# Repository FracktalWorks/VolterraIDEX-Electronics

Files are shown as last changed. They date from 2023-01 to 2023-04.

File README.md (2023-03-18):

# VolterraIDEX-Electronics
Pin Configurations, EagleCAD and gerber files for Volterra IDEX PCBs

The following documentation contains the contents about the pin connections, firmware configurations of the BigTreeTech Octopus V1.1 which is assembled into the VolterraIDEX model of 400x400x370 buildsize.

## Initial Preparation
set jumpers as shown:


Green – Add Jumper

Red – Remove Jumper

1. Insert only the jumper in the Green and remove the other three jumpers in the Red in order to use TMC2209 UART mode.
2. Remove all the jumpers of DIAG to avoid the influence of TMC2209 DIAG on the endstop.
3. Remove the USB 5V power supply jumper to avoid the interaction between the USB 5V of raspberry pi and the DC-DC 5V of the motherboard.
4. Insert all the jumpers into V_FUSED to set the fan voltage to the system supply voltage.
5. Insert the jumper into V_FUSED to set the probe voltage to the system supply voltage.

## Wiring
1. Connect 24V and GND (V+ and V-) from the PSU to PWR and MOTOR_POWER
2. Connect the X(L) Motor (gantry left) to MOTOR0
3. Connect the X(R) Motor (gantry right) to MOTOR1 
4. Connect the E0 (Left Extruder front) motor to MOTOR2_1
5. Connect the E0' (Left Extruder back) motor to MOTOR2_2
6. Connect the Z motor to MOTOR3
7. Connect the Y (gantry left) to MOTOR4
8. Connect the Y1 (gantry right) to MOTOR5
9. Connect the E1 (Right Extruder front) to MOTOR6
10. Connect the E1' (Right Extruder back) to MOTOR7
11. Connect the Extruder0 hot end heater to HE0
12. Connect the Extruder1 hot end heater to HE1
13. Connect the bed SSR (DC Control Side) to HE2
14. Connect the Chamber SSR (DC Control Side) to HE3
Octopus pins and wirings

Bed Heater and Chamber SSR Connections

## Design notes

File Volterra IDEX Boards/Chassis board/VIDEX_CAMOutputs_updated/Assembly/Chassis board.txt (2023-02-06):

Partlist exported from C:/Users/nishb/OneDrive/Documents/GitHub/VolterraIDEX-Electronics/Volterra IDEX Boards/Chassis board/Chassis board.sch at 06-02-2023 11:02

Qty Value                          Device                         Package                    Parts                                                                                                                     Description              
3   FFC/FPC/34PIN/1MMPITCH/TOPLOCK FFC/FPC/34PIN/1MMPITCH/TOPLOCK 34PIN/1MMPITCH/FFC/FPC     K1, K2, K3                                                                                                                                         
1   FRACKTALLOGO                   FRACKTALLOGO                   FRACKTALLOGO               U$2                                                                                                                                                
1   FRAME-LETTER                   FRAME-LETTER                   CREATIVE_COMMONS           FRAME1                                                                                                                    Schematic Frame - Letter 
1   JST-XH-02-PIN-LONG-PAD         JST-XH-02-PIN-LONG-PAD         JST-XH-02-PACKAGE-LONG-PAD X1                                                                                                                        JST XH Connector 2 Pin   
22  TEST-POINTTP_15TH_THRU         TEST-POINTTP_15TH_THRU         TP_15TH                    TP1, TP2, TP3, TP4, TP5, TP6, TP7, TP8, TP9, TP10, TP11, TP12, TP13, TP14, TP15, TP16, TP17, TP18, TP19, TP20, TP21, TP22 SparkFun Test Points

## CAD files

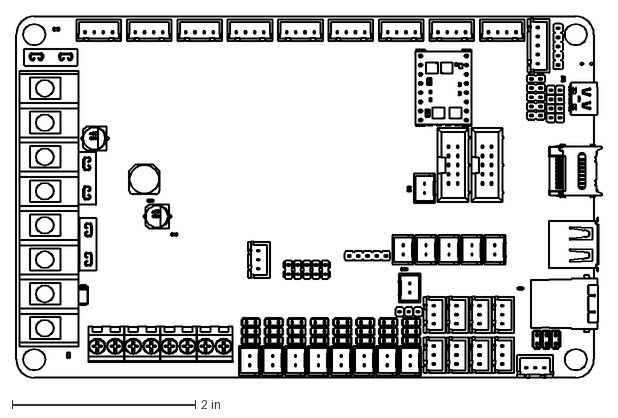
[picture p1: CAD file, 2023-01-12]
BIGTREETECH Octopus V1.0-1.dxf
6.39 x 3.94 in

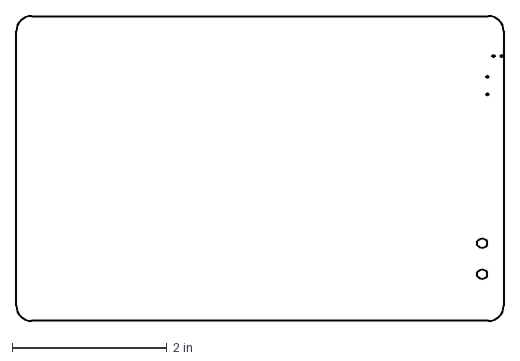
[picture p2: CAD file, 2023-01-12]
BIGTREETECH base Octopus V1.0-1.dxf
6.30 x 3.94 in

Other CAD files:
3D Board/BIGTREETECH Octopus V1.0-1.dwg
3D Board/0411-2.iam
3D Board/1.iam
3D Board/1.ipt
3D Board/1001-3.ipt
3D Board/1001-8.ipt
3D Board/100UF35V.iam
3D Board/2.ipt
3D Board/220UF35V.iam
3D Board/254-3X2.iam
3D Board/254-3X4-1.iam
3D Board/254-4X2.iam
3D Board/266863104.iam
3D Board/2P-254.iam
3D Board/2P-254.ipt
3D Board/3.ipt
3D Board/3P-254.iam
3D Board/4.ipt
3D Board/5.ipt
3D Board/500156144.iam
3D Board/500156144_1.iam
3D Board/500156144_2.iam
3D Board/500156144_3.iam
3D Board/500160368.iam
3D Board/500901-0801_1.ipt
3D Board/5555140-1.iam
3D Board/587257496.iam
3D Board/5P-254.iam
3D Board/5X2P-254.iam
3D Board/6.ipt
3D Board/6641437008.iam
3D Board/6641437328.iam
3D Board/6641440128.iam
3D Board/6641441328.iam
3D Board/6641441568.iam
3D Board/6641441808.iam
3D Board/6641442208.iam
3D Board/6641442768.iam
3D Board/6641443168.iam
3D Board/70314708_1.ipt
3D Board/71071830_1.ipt
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

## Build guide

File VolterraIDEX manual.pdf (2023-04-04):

# USER MANUAL

Disclaimer
Please read the user manual and contents of the instructions carefully. Failing to read the user guide may lead to injuries and damage to Volterra, Industrial 3D Printer. Users of the printer should understand the contents of the manual completely before starting up the Volterra printer**.The methods or conditions used for assembling, handling, storage, use or disposal of the machine are beyond our control or beyond our knowledge. For this reason and other reasons, we do not assume responsibility and explicitly disclaim liability for the loss, injuries, expenses or damage arising out of or in any way connected with the assembly, handling, storage, use or disposal of the product.
The document was made from sources which we believe are reliable. However, the information is provided without any warranty, express or implied, regarding its correctness.

Intended use of Volterra
Volterra 3D Printers are designed and crafted for fused deposition modeling process intended with engineering thermoplastics within a commercial/ business/ research environment. The blend of the precision and speed makes the Volterra 3D printers the perfect machines to conceptualize models, prototypes and small series of production. The printer is coupled with Fracktory Desktop to provide the best experience in slicing with easy interface for the user to change the material properties such that it matches with the machine settings. Fracktory is specifically designed for Volterra printers and gives enhanced experience to the user.
** Volterra printer refers to Volterra family of printers

Preface
This is the installation and user manual for your Volterra 3D printer. This manual contains chapters about the installation and use of the Volterra 3D printer. Important information and instructions on safety, installation and use have been emphasized in this manual. Please read all information and follow the instructions and guidelines in this manual carefully. This ensures that you will obtain great quality prints and that possible accidents and injuries will be prevented. Make sure the user of the Volterra has access to this manual.
Every effort has been made to make this manual complete and accurate as possible. The information is believed to be true but does not aim to be all inclusive and shall be used only as a guide. Kindly bring us the attention on any errors or omissions, so that we can make amendments. Revision and improvement of the documentation could help you serve better.

### Contents

1. Product Details | 2
2. Introduction | 3
3. Getting Started | 5
4. Safety | 7
5. Ancillary Features | 9

### 6. Specifications

11
7. What‘s in the box | 12
8. Setting up | 14
9. Startup process | 17
1O. Downloading and Installing | 27
11. Printing | 31

# WELCOME

# LET’S START

1. PRODUCT DETAILS
Volterra Manual | Page |2

### 1 Product Details

Title: Volterra machine series
Filament diameter: 1.75 mm
Manufacturer: Fracktal Works Pvt Ltd
Manufacturer address: No. 3, 50ft Laggere Main Road Chowdeshwari Nagara, Near Old Police Chowky, Bengaluru, Karnataka, 560 058 Power supply voltage: 200V, 50Hz
Power consumption: 1900W
Working temperature range: 18 °C - 38 °C, indoor use only Working humidity: 85 % or less

2. INTRODUCTION
Volterra Manual | Page |3

### 2 Introduction

Thank you for purchasing our Volterra from Fracktal Works. For correct service of the printer, please read the handbook carefully. All the chapters contain valuable information for the proper service usage.
The user manual is designed specially to make your journey with Volterra printers smooth and hassle free. Fracktal Works welcomes you to the exciting era of 3D printing using Volterra. Read and follow this guide to get the best out of your machine and for an amazing 3D printing experience.

# GETTING STARTED

kknhg

3. GETTING STARTED

### 3 Getting Started

Volterra can print solid 3D models which are simple or complicated ranging from toys to bearings, machine parts, replacements of broken article, casing and variety of other things. Volterra helps turn concepts and ideas into physical prototypes saving time, reducing costs and shortening product development life cycles.
Printing solid 3D objects is an additive manufacturing process which involves a few simple steps. Initially a digital file or a solid model is prepared. This model is then imported into a software commonly known as a ‘Slicer’ and is sliced into layers and fed into the printer to get the model printed. The printer prints by depositing molten material layer by layer with the help of a 3-axis manipulator.

# SAFETY

4. SAFETY

### 4 Safety

### 4.1 Electric Shock Hazards

Never open the access panel when there is power supply to the printer. Before removing the electronics casing always power down the printer completely, Also unplug the power cord connected to the printer. Allow the power supply to discharge for at least one minute.

### 4.2 Burn Hazard

Never touch the extruder nozzle or heater block without turning off the hot end and allowing it to completely cool down naturally. The hot end could take up to twenty minutes to completely cool. Also never touch the plastic which was just extruded. Wait for at least 3 minutes for it to cool down naturally. The plastic can stick to your skin and cause burns. Beware of the heated bed which can reach high temperatures and is capable of causing burns.

### 4.3 Fire Hazard

Never place flammable materials or liquids on or near the printer when powered or in operation.

### 4.4 Pinch Hazard

When the printer is in operation, if placed near the moving parts including the belts, pulleys, or gears, take care of your fingers. Also, tie back long hair or clothing that could get caught in the moving parts of the printer.

### 4.5 Static Charge

Make sure to ground yourself before touching the printer, especially with the electronics. Electrostatic charge can damage electronic components and may affect its functionality. To ground yourself, touch any grounded source.

### 4.6 Age Warning

For users under the age of 18, adult supervision is recommended. Beware of choking hazards.

### 4.7 Fumes and smell Warning

While printing filaments such as ABS, fumes are produced. Do not inhale the fumes because they are toxic in nature. Fumes released could contain toxic substances known as VOC‘s (Volatile Organic compound). Not all VOC‘s are actually toxic, but some may be, especially for younger users. Machine is to be placed in a well ventilated area.

Volterra Manual | Page |7

# ANCILLARY FEATURES

### 5. ANCILLARY FEATURES

### 5 Ancillary Features

5. 1 HEPA Filter

HEPA filter is mounted on the central rear panel of the machine which is mechanically convicting the air through a fine mesh that traps harmful particulate air.

### 5.2 IDEX technology

IDEX is the extrusion system capable of printing with two heads independently. This allows enabling Duplication and Mirror printing modes capable of printing two pieces at a time. Double printing capacity means double productivity, all with the same investment.

### 5.3 Chamber heaters

Chamber heaters enables users to print in high temperature filaments, such as PEEK and ULTEM which need a stable chamber temperatures.

### 5.4 Filament heaters

Filament materials such as PVA absorbs moisture when stored in open atmosphere. It is essential for PVA to be preheated before giving print. Instead of preheating externally, filament heater eliminates the use of external heating.

### 5.5 Light Tower

Stack lights are used in a variety of machines and process environments. Color codes for our machine is as follows:

- Green indicates “Printing"
- Amber indicates “Operational/ Idle"
- Red indicates “Error/ Offline / any other issue"

# Specification & what’s in

# the box!

6. SPECIFICATIONS

### 6 Specifications

| Parameters | Speed | IDEX | HT
- | Technology | FDM/FFF | FDM/FFF | FDM/FFF
- | Model Materials | PLA, ABS, Nylon Flexible** | PLA, PVA, ABS, HIPS, Flexible** | PLA, ABS, Nylon, ULTEM, PEEK, Flexible**
- | Layer Resolution | 100 – 450 um | 100 – 450 um | 100 – 450 um
- | Positioning Accuracy Z | 5 um | 5 um | 5 um
- | Positioning Accuracy X-Y | 10 um | 10 um | 10 um
- Max. Print Size Heated
| With “Magnalock Build Substrate” | 380x400x400 mm | 380x400x400 mm | 380x400x400 mm
- | Chamber Heater | Yes (120C) | Yes (120C) | Yes (150C)
- | Filament Heater | Yes (60C) | Yes (60C) | Yes (60C)
- | Camera | Live Camera for 5MP | Live Camera for 5MP | Live Camera for 5MP
- | Heated Bed | Yes (120C) | Yes (120C) | Yes (150C)*
- | Max. Nozzle temperature | 250C | 250C | 450C
- | Door Sensor | Yes (Active Detection) | Yes (Active Detection) | Yes (Active Detection)
- | Nozzles*** | 1 (0.6mm Default) | 2 (0.6mm Default) | 2 (0.6mm Default)
- | File Type | STL, OBJ, G-Code | STL, OBJ, G-Code | STL, OBJ, G-Code
- | HEPA Filter | Yes | Yes | Yes
- | Power | 240V, 60Hz, 1900W* | 240V, 60Hz, 1900W* | 240V, 60Hz, 1900W*
- 7” “Mission Control:
| Touch” Panel | Touch HMI | Touch HMI | Touch HMI
- Tower Light Indication
| and Emergency Stop Switch | Yes | Yes | Yes
- | Interface Connectivity | USB, Wi-Fi, Ethernet | USB, Wi-Fi, Ethernet | USB, Wi-Fi, Ethernet

*Specification tend to change as per design
** Machine ships with Brass-0.6mm nozzles Extra nozzles(0.25, 0.4, 0.6, 0.8) are charged additionally. Nozzle material with Hardened Steel and Stainless Steel variants are also available
*** Compatible with Fracktal Works Flex series of Filaments
**** Comprehensive warranty covers all parts except nozzle assembly, accessory box tools and consumables

7. WHAT‘S IN THE BOX

### 7 What‘s in the box

(a) Light tower
(b) Hotend and Nozzle kits*
(c) Filament*
(d) Camera*

Accessories Checklist

1. Flex Build Plate attached to the bed
2. Allen Keys (2, 2.5, 3 mm size)
3. Print Adhesive
4. WD 40 Spray
5. USB drive
6. Nozzle cleaning tool or stove pin
7. Power cord
8. Sharp Tweezers
9. Filament cutter

*Few accessories are subjected to purchase order

# SETTING

UP

8. SETTING UP

### 8 Setting up

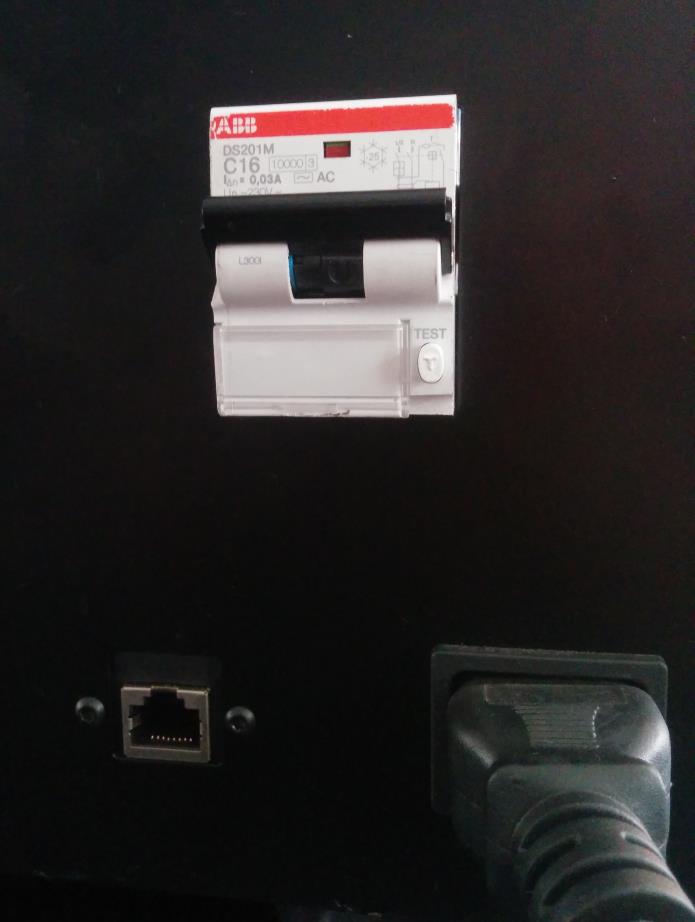
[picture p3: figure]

Figure 8.1: RCBO contactor with socket

The power cord has to be connected to the IEC socket located at the backside in the bottom left of the printer near the power socket. Connect the power cable to the 220V wall socket and flip the contactor (RCBO) to turn the printer ON.
After turning the printer ON, turn the button switch ON which is located on front panel of the printer. An LED should light up after pressing the switch. LED lighting can signify the power state of the printer. When the button switch is in pressed condition, it signifies the printer is in ON condition also showing with ON state of the LED on the button switch. On the other way, when the button switch is in released position, the LED light should go OFF and state the turned off condition.
By turning the two switches, the printer should boot up and the display should show the booting. Make sure the emergency stop button is in release position.
The E-stop or the Kill switch turns off the whole machine. This switch is a handy add-on in case
of emergency.
In case, you want the printer to be connected to a wired LAN connection, the LAN cable can be connected to the LAN port present just beside the power socket.

8. SETTING UP

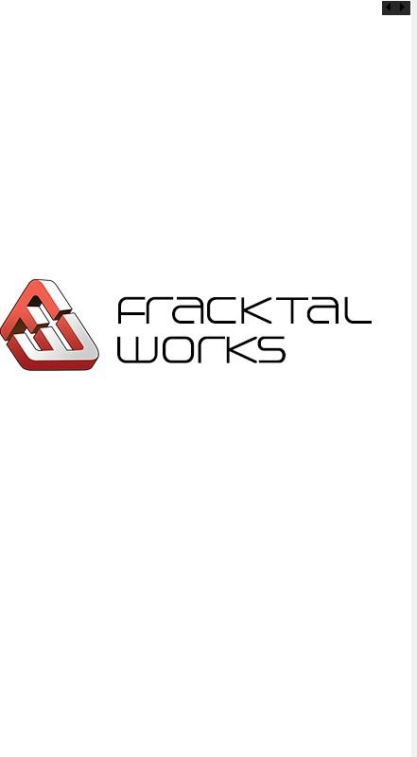
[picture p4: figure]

Figure 8.2: Fracktal Works Loading Screen .

# STARTUP PROCESS

9. STARTUP PROCESS

### 9 Startup process

After turning on the power supply for Volterra, the LCD screen will get activated. The following section of the manual will guide you through the process of loading the filament, leveling the print plate and testing your first build.
First you mount the magnetic print plate on the bed and it will automatically stick to it. Note that the slits on the build plate (highlighted) pass through the mounts on the bed.

Figure 9.1: Build surface aligning with the slits/notches on bed

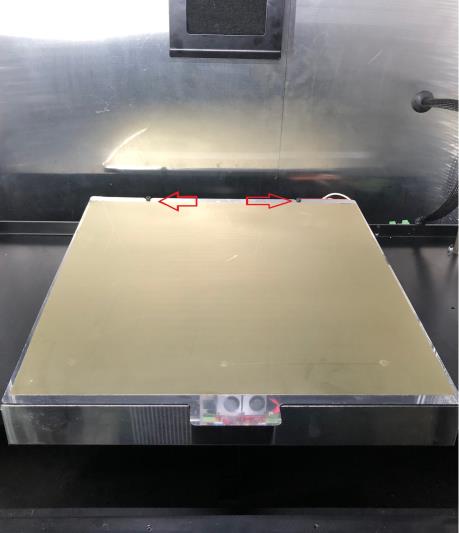
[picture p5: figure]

Figure 9.2: Build surface placed on the bed

Your bed should ultimately look something like this.

9. STARTUP PROCESS
9. 1 Loading Filament

To load a new filament, select the control option from the main menu and click on the following icon.

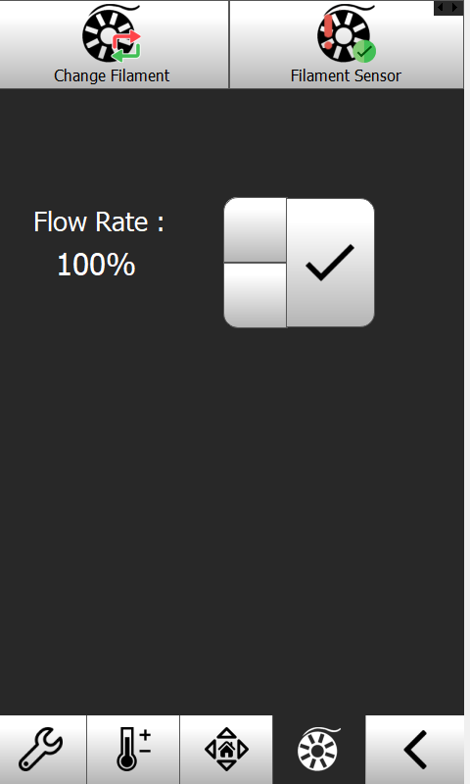
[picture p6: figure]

Figure 9.3: Change filament control

9. STARTUP PROCESS

Figure 9.4: change filament button

Press on the ‘change filament’ button on corner as shown in fig. 9.4.
If you have VolterraIDEX, the filament change wizard screen should look something like the image shown in fig 9.5.

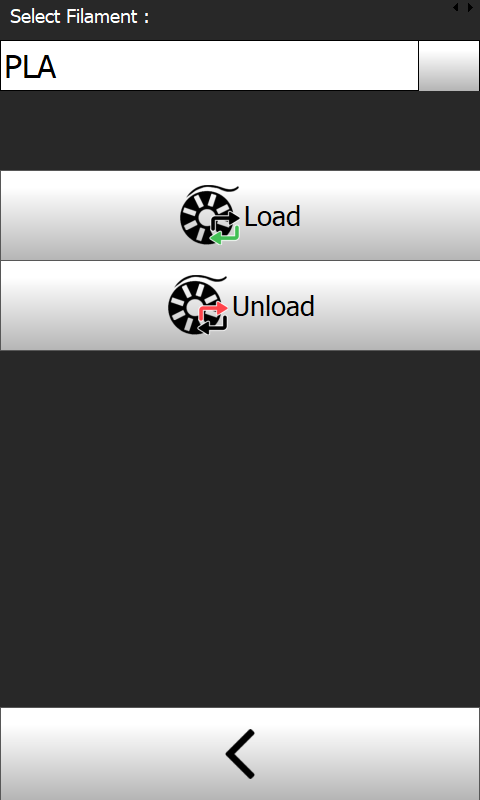
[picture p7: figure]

Figure 9.5: Change filament menu for VolterraIDEX

9. STARTUP PROCESS

Figure 9.6: Change filament menu for VolterraIDEX

From the drop down menu under "Select Filament", select the filament which you want to load and tap on Load button.
If you have VolterraIDEX (Fig 9.6), the filament change wizard screenshould look something like the image above.

9. STARTUP PROCESS

From the drop down menu under "Select Filament", select the filament which you want to load. Also select the nozzle into which you want to insert the filament and tap on Load button. For example, if you want to print PLA. Select PLA from the select drop down menu.
If the old filament is already loaded, then press the unload icon and when the filament is out press the load filament icon to insert the new filament. You can tap on unload again for unloading the filament in case the filament is not unloaded in one tap.

9. STARTUP PROCESS

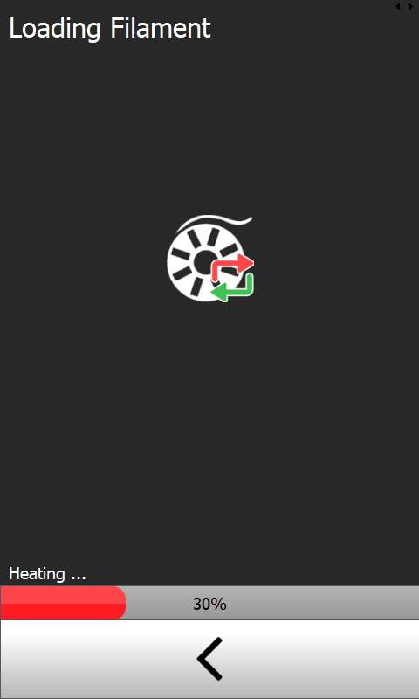
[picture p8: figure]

Figure 9.8: Change filament Heating process

When you press the load icon the printer should start heating the extruder to facilitate the loading of the filament and the window should look like the image shown above as per fig 9.8.
Once the extruder is heated according to the type of filament required, another window should appear which looks like the image shown in fig 9.9.

9. STARTUP PROCESS

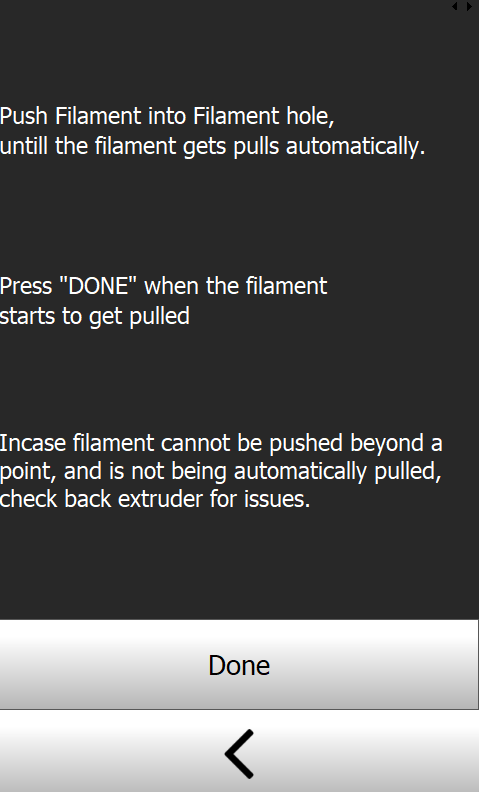
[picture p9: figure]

Figure 9.9: Change Filament Heating Process

In this window, Insert the filament into the channel present in the filament chamber. The left side channel is for EXT0 and the right side channel is for EXT1. Keep pushing into the channel and the PTFE till it reaches the back side extruder motor and gets pulled by it automatically, since the motor keeps rotating continuously. If the filament does not get pulled despite pushing to its limit, do check the back extruder to check if any issues persists such as, getting stuck in the PTFE or getting stuck in the motor arm.
After the Filament gets pulled successfully, press “DONE” on the screen. The filament gets pulled with a faster federate.

9. STARTUP PROCESS

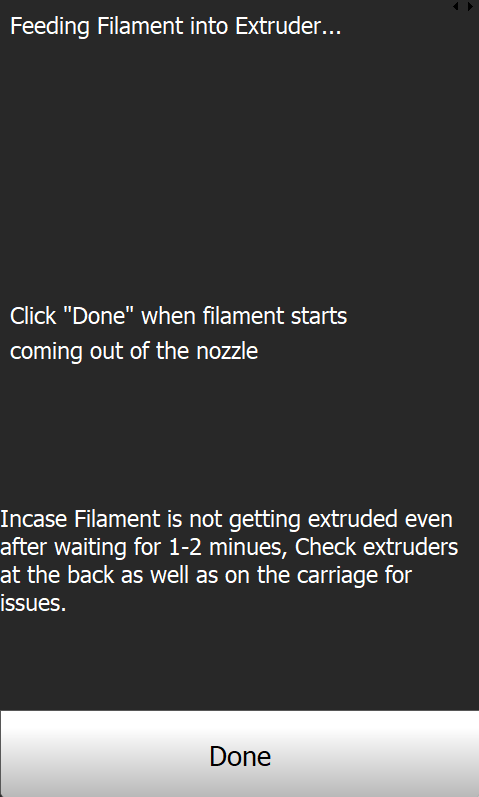
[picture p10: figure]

Figure 9.10: Change Filament Heating Process #2

When the filament gets pulled with a faster federate, and when the filament starts coming out of the nozzle, click on “DONE”. In cases when the filament does not come out of the nozzle waiting for approximately 1 – 2 minutes, do check the extruders at the back and as well as the carriage extruders if any issues persists.

9. STARTUP PROCESS

### 9.2 Levelling the bed

Importance of bed levelling
Volterra has gone through the process of bed levelling at Fracktal Works. However, there is a
chance that the alignment is disturbed during the transportation and unboxing process.
If the extruder nozzle is too far from the build platform, or if all parts of the build plate are not at the same distance from the nozzle while printing, then the build will not attach properly on the build surface. If the extruder nozzle is too close to the build platform, then the filament might be prevented from being extruded and it could also lead to scratches on the build plate.

Levelling the build plate ensures that the objects you print adhere well to the build plate, to give you a hassle free and smooth experience.
The Process of Levelling and Testing your first print
Note: Make sure there is no plastic sticking out of the nozzle. It is recommended to heat the nozzle and remove any excess plastic using supplied tweezers before continuing.
To initiate Bed Levelling, on the home screen, click on | icon to open the main menu.

9. STARTUP PROCESS

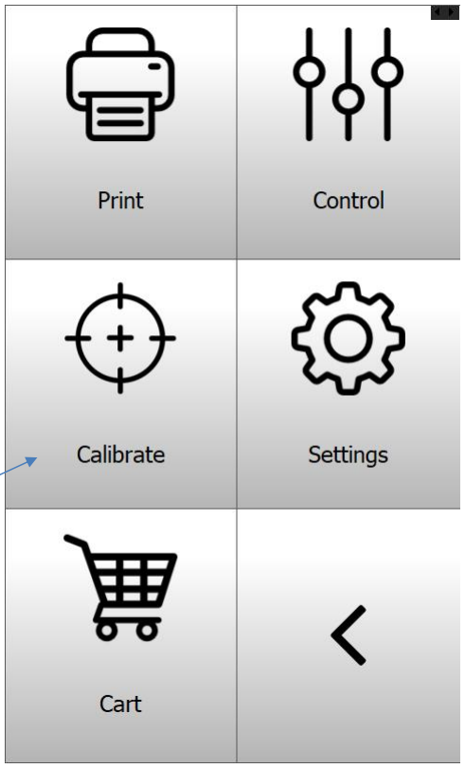
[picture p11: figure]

Figure 9.10: Main Menu

From there select the menu icon, after clicking on the menu icon, a new screen should come up
which looks like the image shown above. From the menu select the Calibrate icon and that will take you to the calibration panel. The calibration panel should look like in Fig 9.11.

9. STARTUP PROCESS

Figure 9.11: Main Menu

From that screen select the Calibration Wizard option and follow the on screen instructions that follow up
and you will have a perfectly leveled bed for your printer.

# DOWNLOADING AND INSTALLING

10. DOWNLOADING AND INSTALLING

### 1O Downloading and Installing

The preferred software for your Volterra printer is Fracktory 3 from Fracktal Works. This software package converts your 3D model(STL file) into instructions(G-code file) that your Volterra requires to produce an object.

- The Fracktory software package can be downloaded from fracktal.in
- Download the latest version of Fracktory for your operating system.
- Note: You will require a 64 bit system to run Fracktory.
- Open the installer and follow the directions to install the software.
- After installing Fracktory, open the application to configure the software to your 3D printer.

1O.1 Adjusting the model

There are various ways to manipulate the object before printing like rotation, scaling and mirroring along axis.

1O.1.1 Rotate

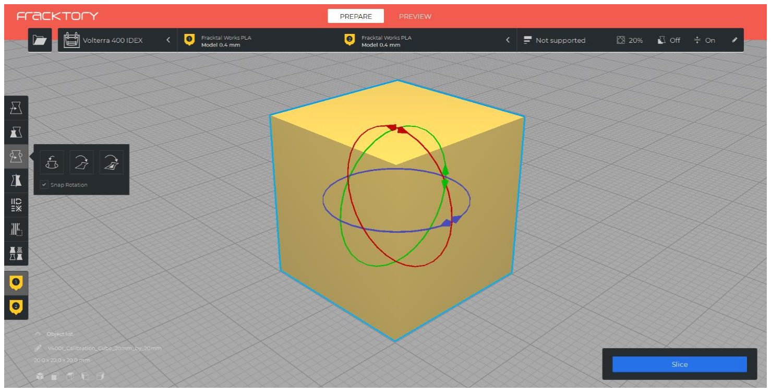
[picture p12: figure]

Figure 10.1: Fracktory rotate option

The icon on the left side shows the rotate button; it allows you to rotate the model in the X, Y or Z axes. By selecting one of the axes and on moving your mouse, you can rotate the object with an angleof 15 degrees.

10. DOWNLOADING AND INSTALLING

You can also rotate the object with an angle of 1 degree by holding the “Shift” Key.
Once the rotate button has been selected a few more options will pop up just above the rotate button. The “Reset” button offers the possibility to resets the model to its original position. By using the “Lay flat” option your model will be placed flat on the surface of the build plate. This can become handy when your model doesn’t have a completely flat surface or when it doesn’t load correctly in Fracktory. The model will be placed on the face closest to the build plate.

1O.1.2 Scale

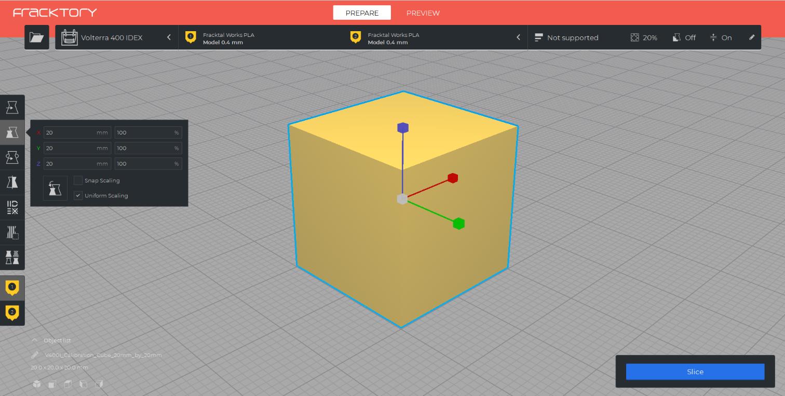
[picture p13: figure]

Figure 10.2: Fracktory scale option

The middle icon is the Scale button. This option can be used to change the dimensions of the model in X, Y and Z direction. Scaling can be done by clicking and dragging the (square) scaling icons that appear on the model, or by changing the numeric values that appear in the box just above the "Scale" button. You can either use a scale factor to change the dimensions or enter the exact size. A model will be scaled in all directions, simultaneously by default, but you can unmark “Uniform scale” in order to scale in each direction independently. Furthermore a “Reset” and “Scale to max” button will be shown above the Scale button. The Reset button allows you to reset the model to its original dimensions. By using the Scale to max option, the model will be scaled to the maximum size that fits in the machine.

10. DOWNLOADING AND INSTALLING

1O.1.3 Mirror

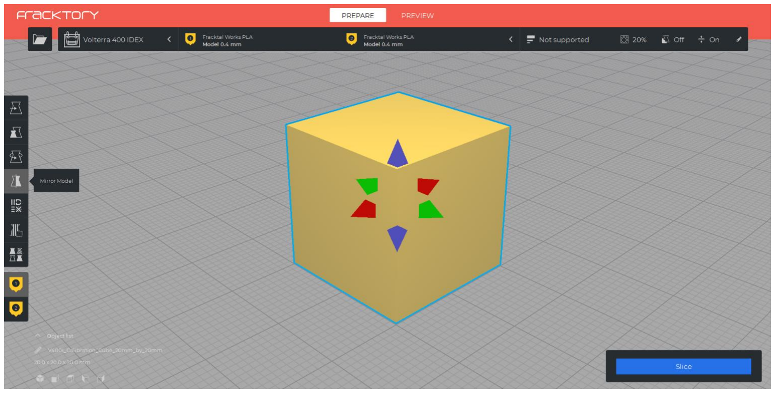
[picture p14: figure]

Figure 10.3: Fracktory mirror option

The right most icon at the bottom is the “Mirror” button. This can be used to flip the model in either the X, Y or Z direction.

# PRINTING

11. PRINTING

### 11 Printing

Now that you have installed and configured Fracktory, you can print your first part. Some sample files are provided in the supplied SD card. Fracktory uses millimeters as the base unit. When adding any files please check that the units are correct by clicking on the scale button.

Click the load Button and select the required “.STL” file for printing.
Now your object will be placed in center. You can manipulate the object using move, scale, rotate etc.

Figure 11.1: Fracktory loaded with STL for printing

Whenever you load a model, adjust a model or change settings, Fracktory starts processing the file on-the-fly.

You can see its progress below save G-code button. G-code is the processed file requiredby the machine to print your 3D object. When the file is processed you click the save G-code button. If you have inserted a SD card then the button turns into a SD card button. This will load the G-code directly into the SD card. Beware that it will overwrite the previous file of same name without warning.
When G-code file is generated it is saved on your system and can be used to print using Wi-Fi or USB mass storage device

11. PRINTING

If Printing from Wi-Fi then follow the below steps

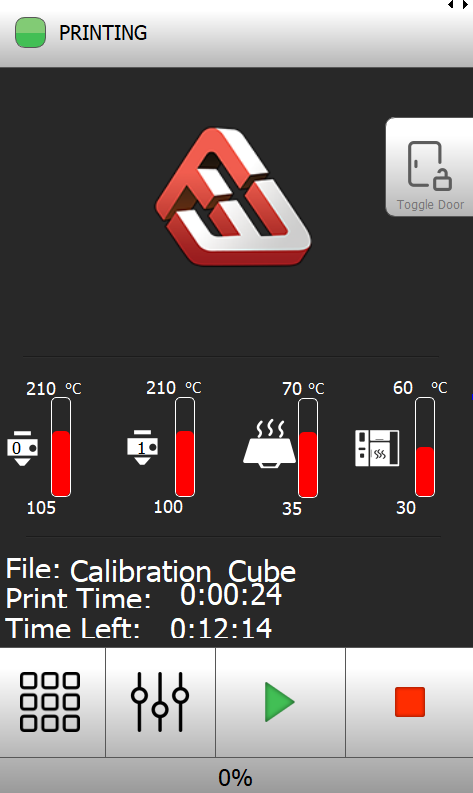
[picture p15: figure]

Figure 11.2: printing

When running the printer for the first time select the menu bar from the main screen. Open and select the settings icon in it.

11. PRINTING

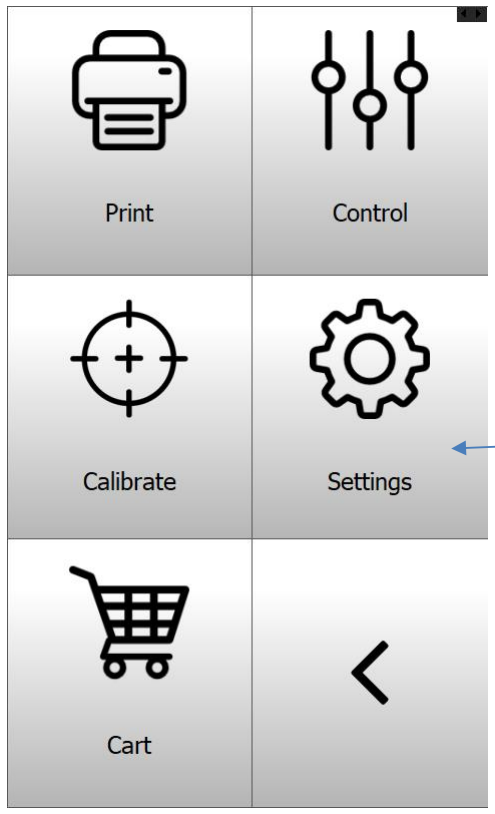
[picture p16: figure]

Figure 11.3: Menu UI in printer

When you select the settings icon, this window should open Then click on Configure Wi-Fi icon (in Figure 11.3)

11. PRINTING

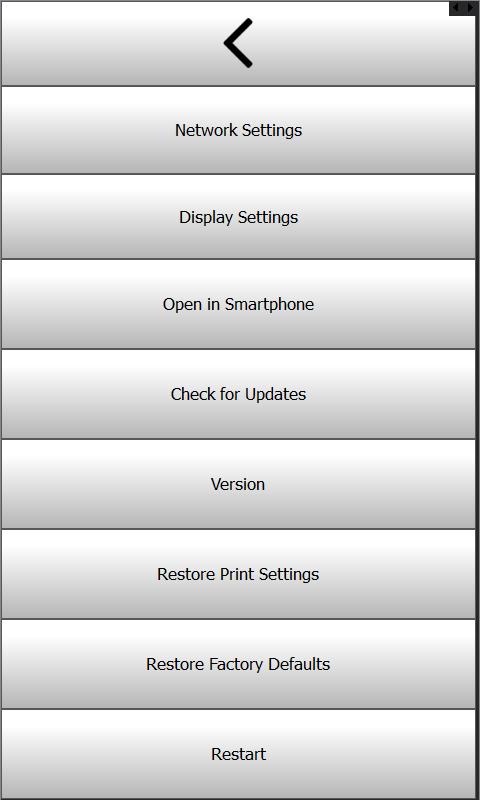
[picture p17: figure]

Figure 11.4: Setting UI in printer

When you click on configure Wi-Fi option, a new window should pop up which should look like the above Figure 11.4.

11. PRINTING

Figure 11.5: Wi-Fi setting UI in the printer

Choose your SSID Wi-Fi access point name and then click on the space provided to enter the password using the onscreen keyboard. This will take you back to the previous window.

Figure 11.6: Keyboard to type the password for SSID

Now the configure window should look something like this

11. PRINTING

Figure 11.7: Wi-Fi configuration on typing the password

Press done if the SSID and password are correct. You will be brought back to the settings menu once you are connected and then next step is to click on the network info icon in the settings menu

Figure 11.8: Network Info button in settings

This should take you to a new page that has your Printer’s IP address and the window should look like the image below.
Note down your printer’s IP, it changes whenever you connect to a new network so make sure to visit network info to know your printer’s IP address. Now let’s focus on the system which has your G-code file generated from Fracktory.

11. PRINTING

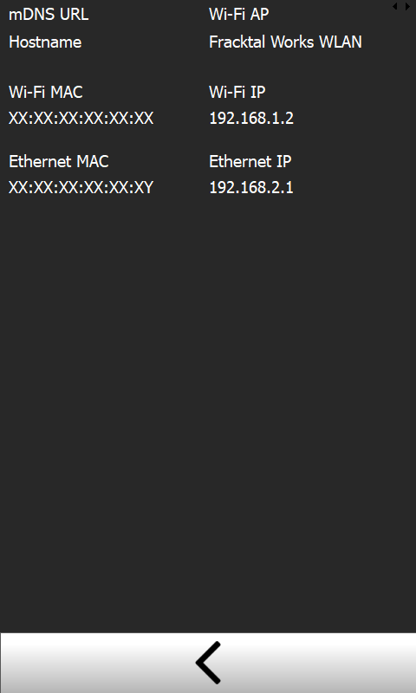
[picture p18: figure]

Figure 11.9: Network Info

NOTE: The printer and the computer are connected to same network in order to access the printer through the computer.
Then open your systems browser and enter your printer’s IP address which you had noted in the previous step.

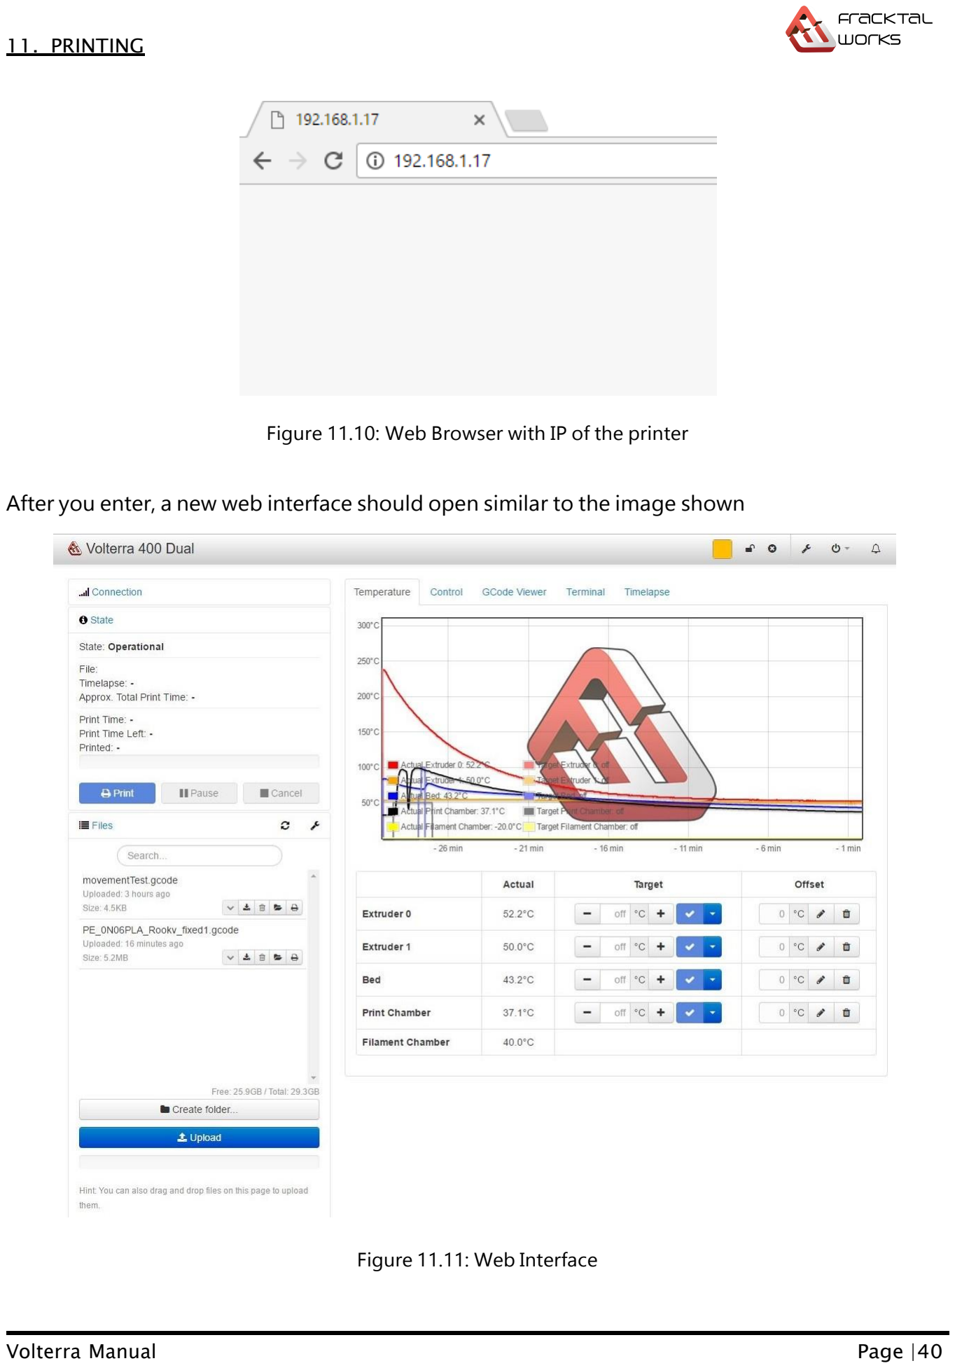
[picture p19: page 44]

11. PRINTING

Figure 11.10: Web Browser with IP of the printer

After you enter, a new web interface should open similar to the image shown

Figure 11.11: Web Interface

11. PRINTING

To upload the G-code press the upload on the left corner of your screen.

Figure 11.12: Upload icon on Web Interface

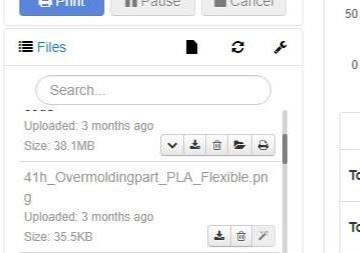
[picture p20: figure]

Figure 11.13: Load section on Web Interface

After clicking upload you have to locate and select the G-code file on your system and upload. After your file is uploaded you can see it in the uploaded files menu.

Figure 11.14: Load section on Web Interface

After that press the load icon below the uploaded file. The icon looks like a folder.
Once the file is loaded to the printer via Wi-Fi, it will be shown in the status menu of the printer which is present on the top right corner of the screen. The Connection icon shows that the

11. PRINTING

connection is established between printer and system. Now you can hit the print button and start your print directly.

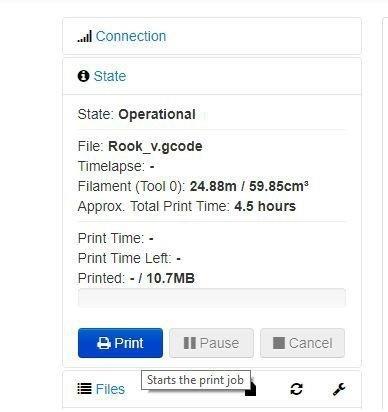
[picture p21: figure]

Figure 11.15: Status of the printer on Web Interface

The graphical representation in the center of the page shows all the vitals of the printer in graphical form which includes the temperature of both nozzles and bed and their target temperature.

11. PRINTING

Figure 11.16: Temperature status of the printer on Web Interface

To change the Individual temperature of both the nozzles and bed you can use the option below the graph.

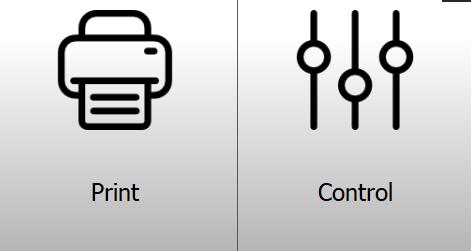
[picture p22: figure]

Figure 11.17: Standalone print menu on printer

After you have uploaded the file, if you have have not given the print command from the web interface already, then you can also give the print command on the machine itself by clicking on the menu icon on the main screen of the printer and clicking on the print icon in the menu.

11. PRINTING

Then it will ask you to select whether you want to print from the internal memory of the printer or from an USB mass storage device connected to the printer.

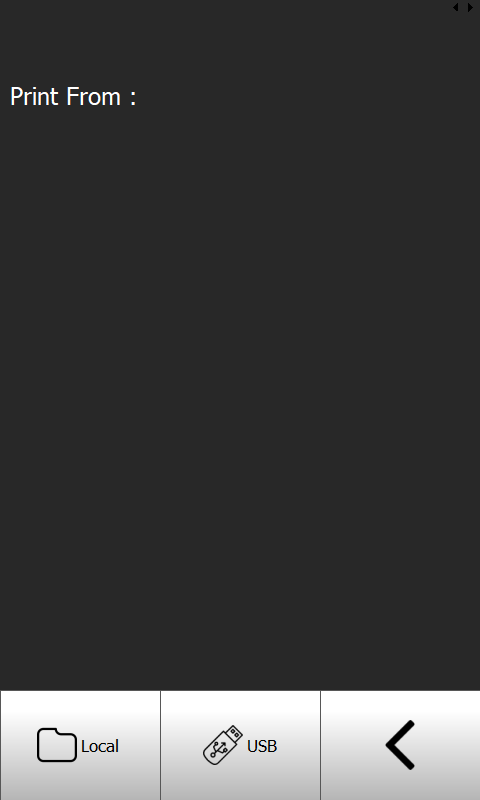
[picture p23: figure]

Figure 11.18: Standalone printing on printer

First let’s see printing from internal memory of the printer.

11. PRINTING

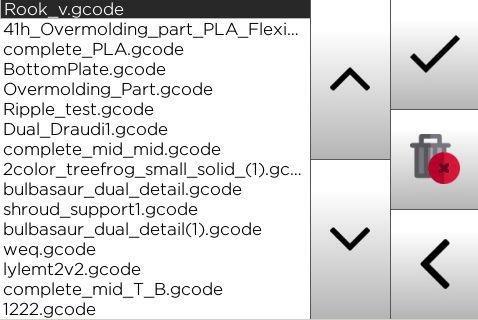
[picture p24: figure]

Figure 11.19: G-code on printer

Selecting the local icon will take you to the G-code files stored in the internal memory, you need to select the file you just uploaded from the web interface and click on the tick which will take you to the confirmation screen.
Click on the tick icon to confirm after which the print starts.

11. PRINTING

Figure 11.20: G-code on USB

Now let’s see how to print using USB mass storage device
Copy the G-code file in your mass storage device and plug the pen drive to the printer and instead of selecting local, select USB which will take you to the file explorer where you can see all G-code files present in your mass storage device. Select the G-code and transfer the file to the local memory and then issue the print.

11. PRINTING

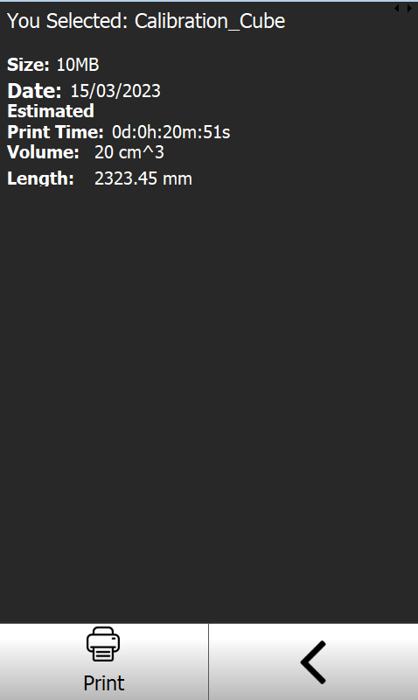
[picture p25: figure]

Figure 11.21: Print confirmation screen

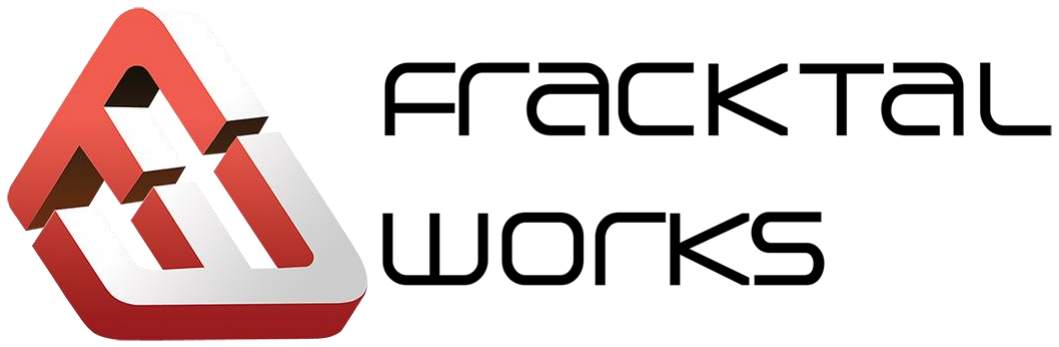
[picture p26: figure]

Contact us: https://care.fracktal.in

for more information visit www.fracktal.in Address: No. 3, 50ft Laggere Main Road, Chowdeshwari Nagara, Near Old Police Chowky, Bengaluru 560 058

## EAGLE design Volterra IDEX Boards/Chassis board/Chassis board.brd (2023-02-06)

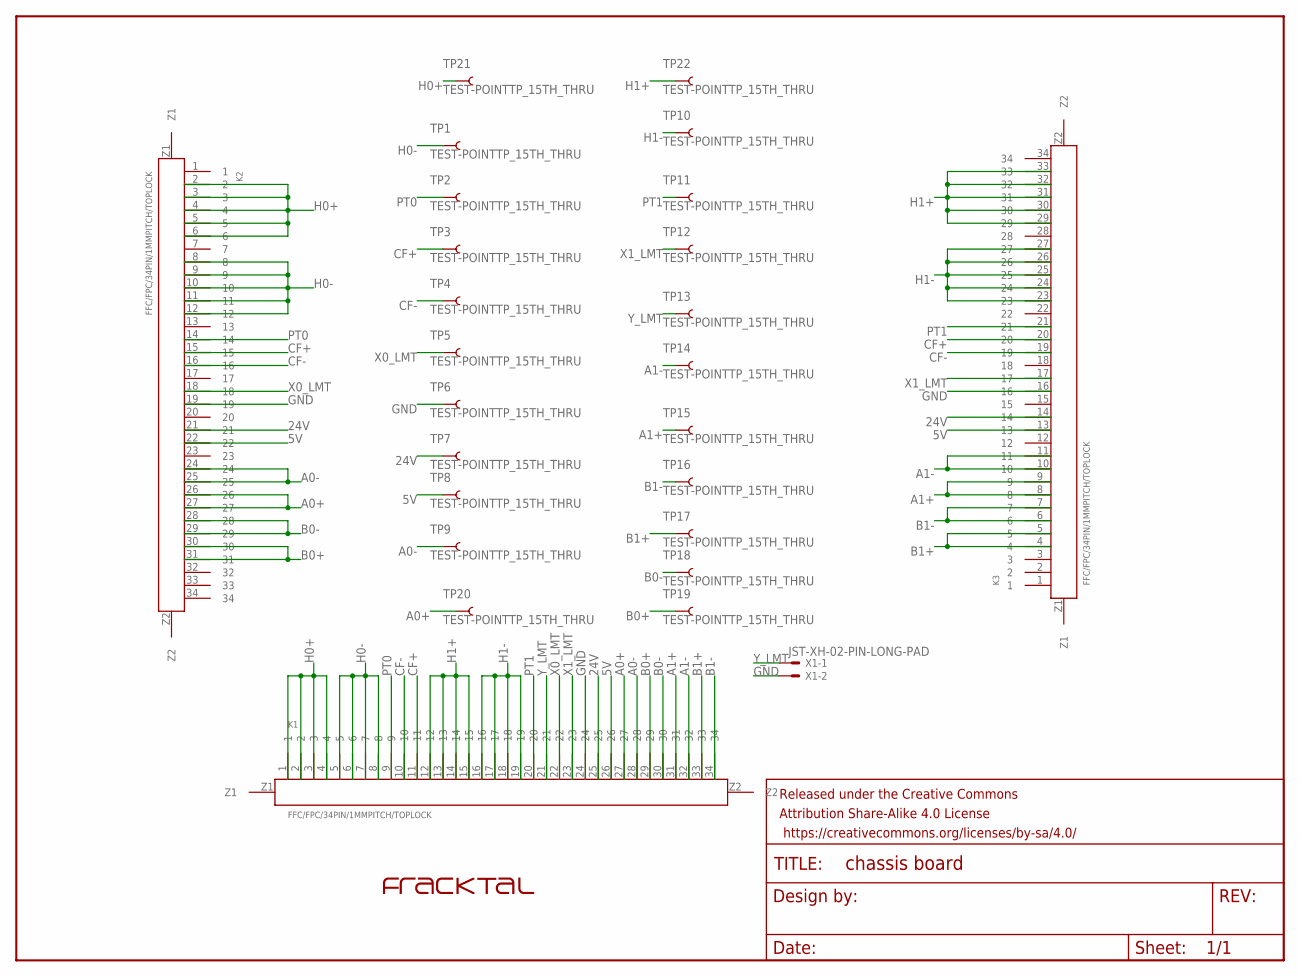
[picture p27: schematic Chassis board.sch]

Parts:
FRAME1: FRAME-LETTER; CREATIVE_COMMONS
K1, K2, K3: FFC/FPC/34PIN/1MMPITCH/TOPLOCK; 34PIN/1MMPITCH/FFC/FPC
TP1, TP2, TP3, TP4, TP5, TP6, TP7, TP8, TP9, TP10, TP11, TP12, TP13, TP14, TP15, TP16, TP17, TP18, TP19, TP20, TP21, TP22: TEST-POINTTP_15TH_THRU; TP_15TH
U$2: FRACKTALLOGO
X1: JST-XH-02-PIN-LONG-PAD; JST-XH-02-PACKAGE-LONG-PAD

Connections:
5V: K1.26, K2.22, K3.13, TP8.P$1
24V: K1.25, K2.21, K3.14, TP7.P$1
A0+: K1.27, K2.26, K2.27, TP20.P$1
A0-: K1.28, K2.24, K2.25, TP9.P$1
A1+: K1.31, K3.8, K3.9, TP15.P$1
A1-: K1.32, K3.10, K3.11, TP14.P$1
B0+: K1.29, K2.30, K2.31, TP19.P$1
B0-: K1.30, K2.28, K2.29, TP18.P$1
B1+: K1.33, K3.4, K3.5, TP17.P$1
B1-: K1.34, K3.6, K3.7, TP16.P$1
CF+: K1.11, K2.15, K3.20, TP3.P$1
CF-: K1.10, K2.16, K3.19, TP4.P$1
GND: K1.24, K2.19, K3.16, TP6.P$1, X1.2
H0+: K1.1, K1.2, K1.3, K1.4, K2.2, K2.3, K2.4, K2.5, K2.6, TP21.P$1
H0-: K1.5, K1.6, K1.7, K1.8, K2.8, K2.9, K2.10, K2.11, K2.12, TP1.P$1
H1+: K1.12, K1.13, K1.14, K1.15, K3.29, K3.30, K3.31, K3.32, K3.33, TP22.P$1
H1-: K1.16, K1.17, K1.18, K1.19, K3.23, K3.24, K3.25, K3.26, K3.27, TP10.P$1
PT0: K1.9, K2.14, TP2.P$1
PT1: K1.20, K3.21, TP11.P$1
X0_LMT: K1.22, K2.18, TP5.P$1
X1_LMT: K1.23, K3.17, TP12.P$1
Y_LMT: K1.21, TP13.P$1, X1.1

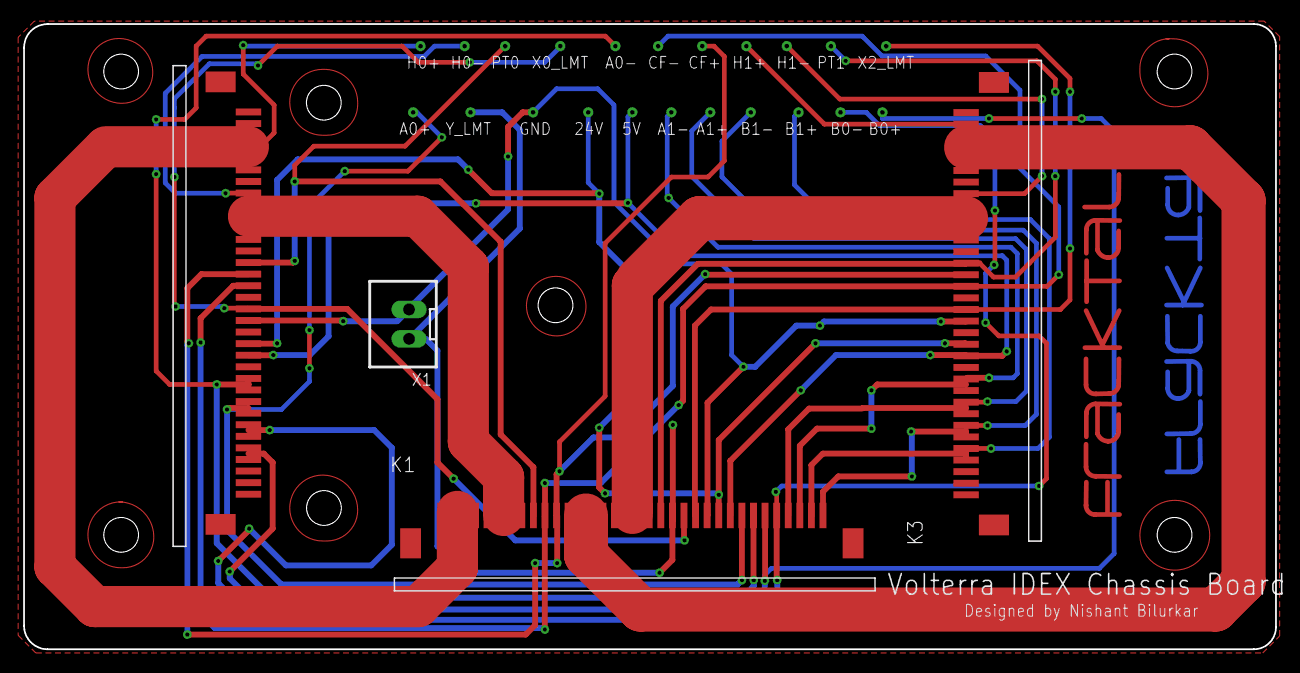
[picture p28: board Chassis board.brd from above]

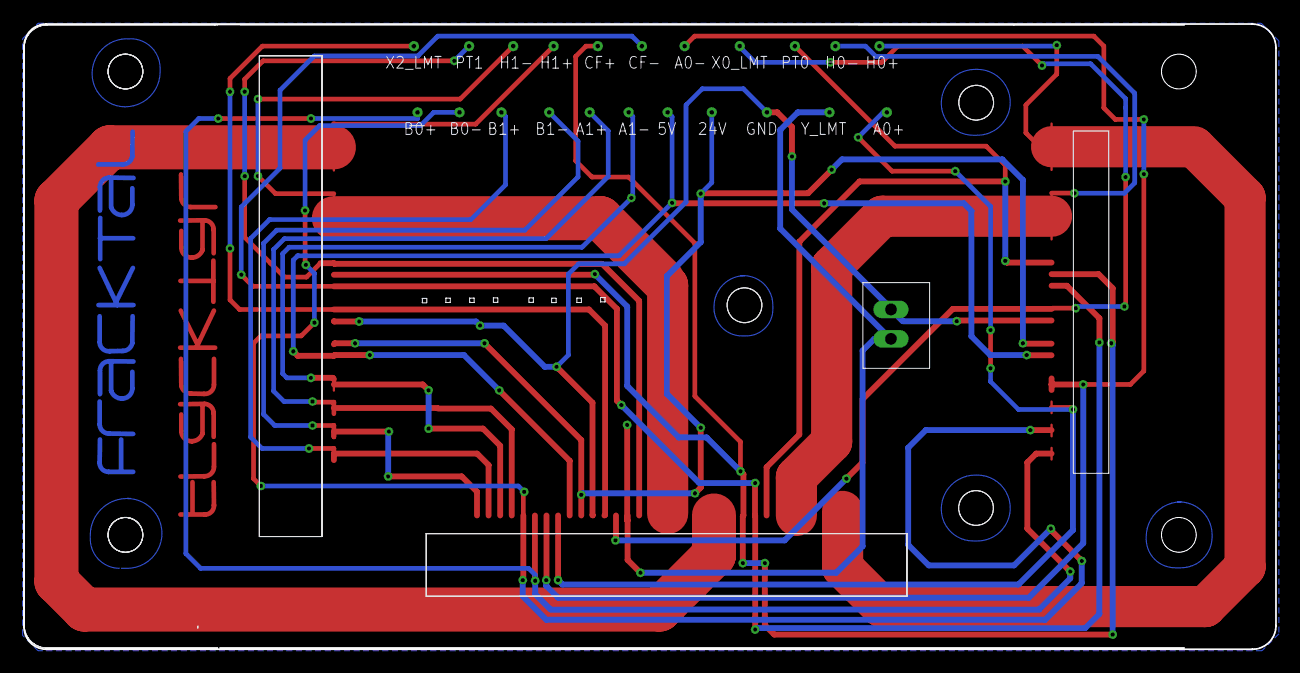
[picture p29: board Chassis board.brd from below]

Board: 2 copper layers, 108.1 x 54.0 mm, 29 parts (23 on the bottom side), 22 nets.

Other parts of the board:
U$3: FRACKTALLOGO

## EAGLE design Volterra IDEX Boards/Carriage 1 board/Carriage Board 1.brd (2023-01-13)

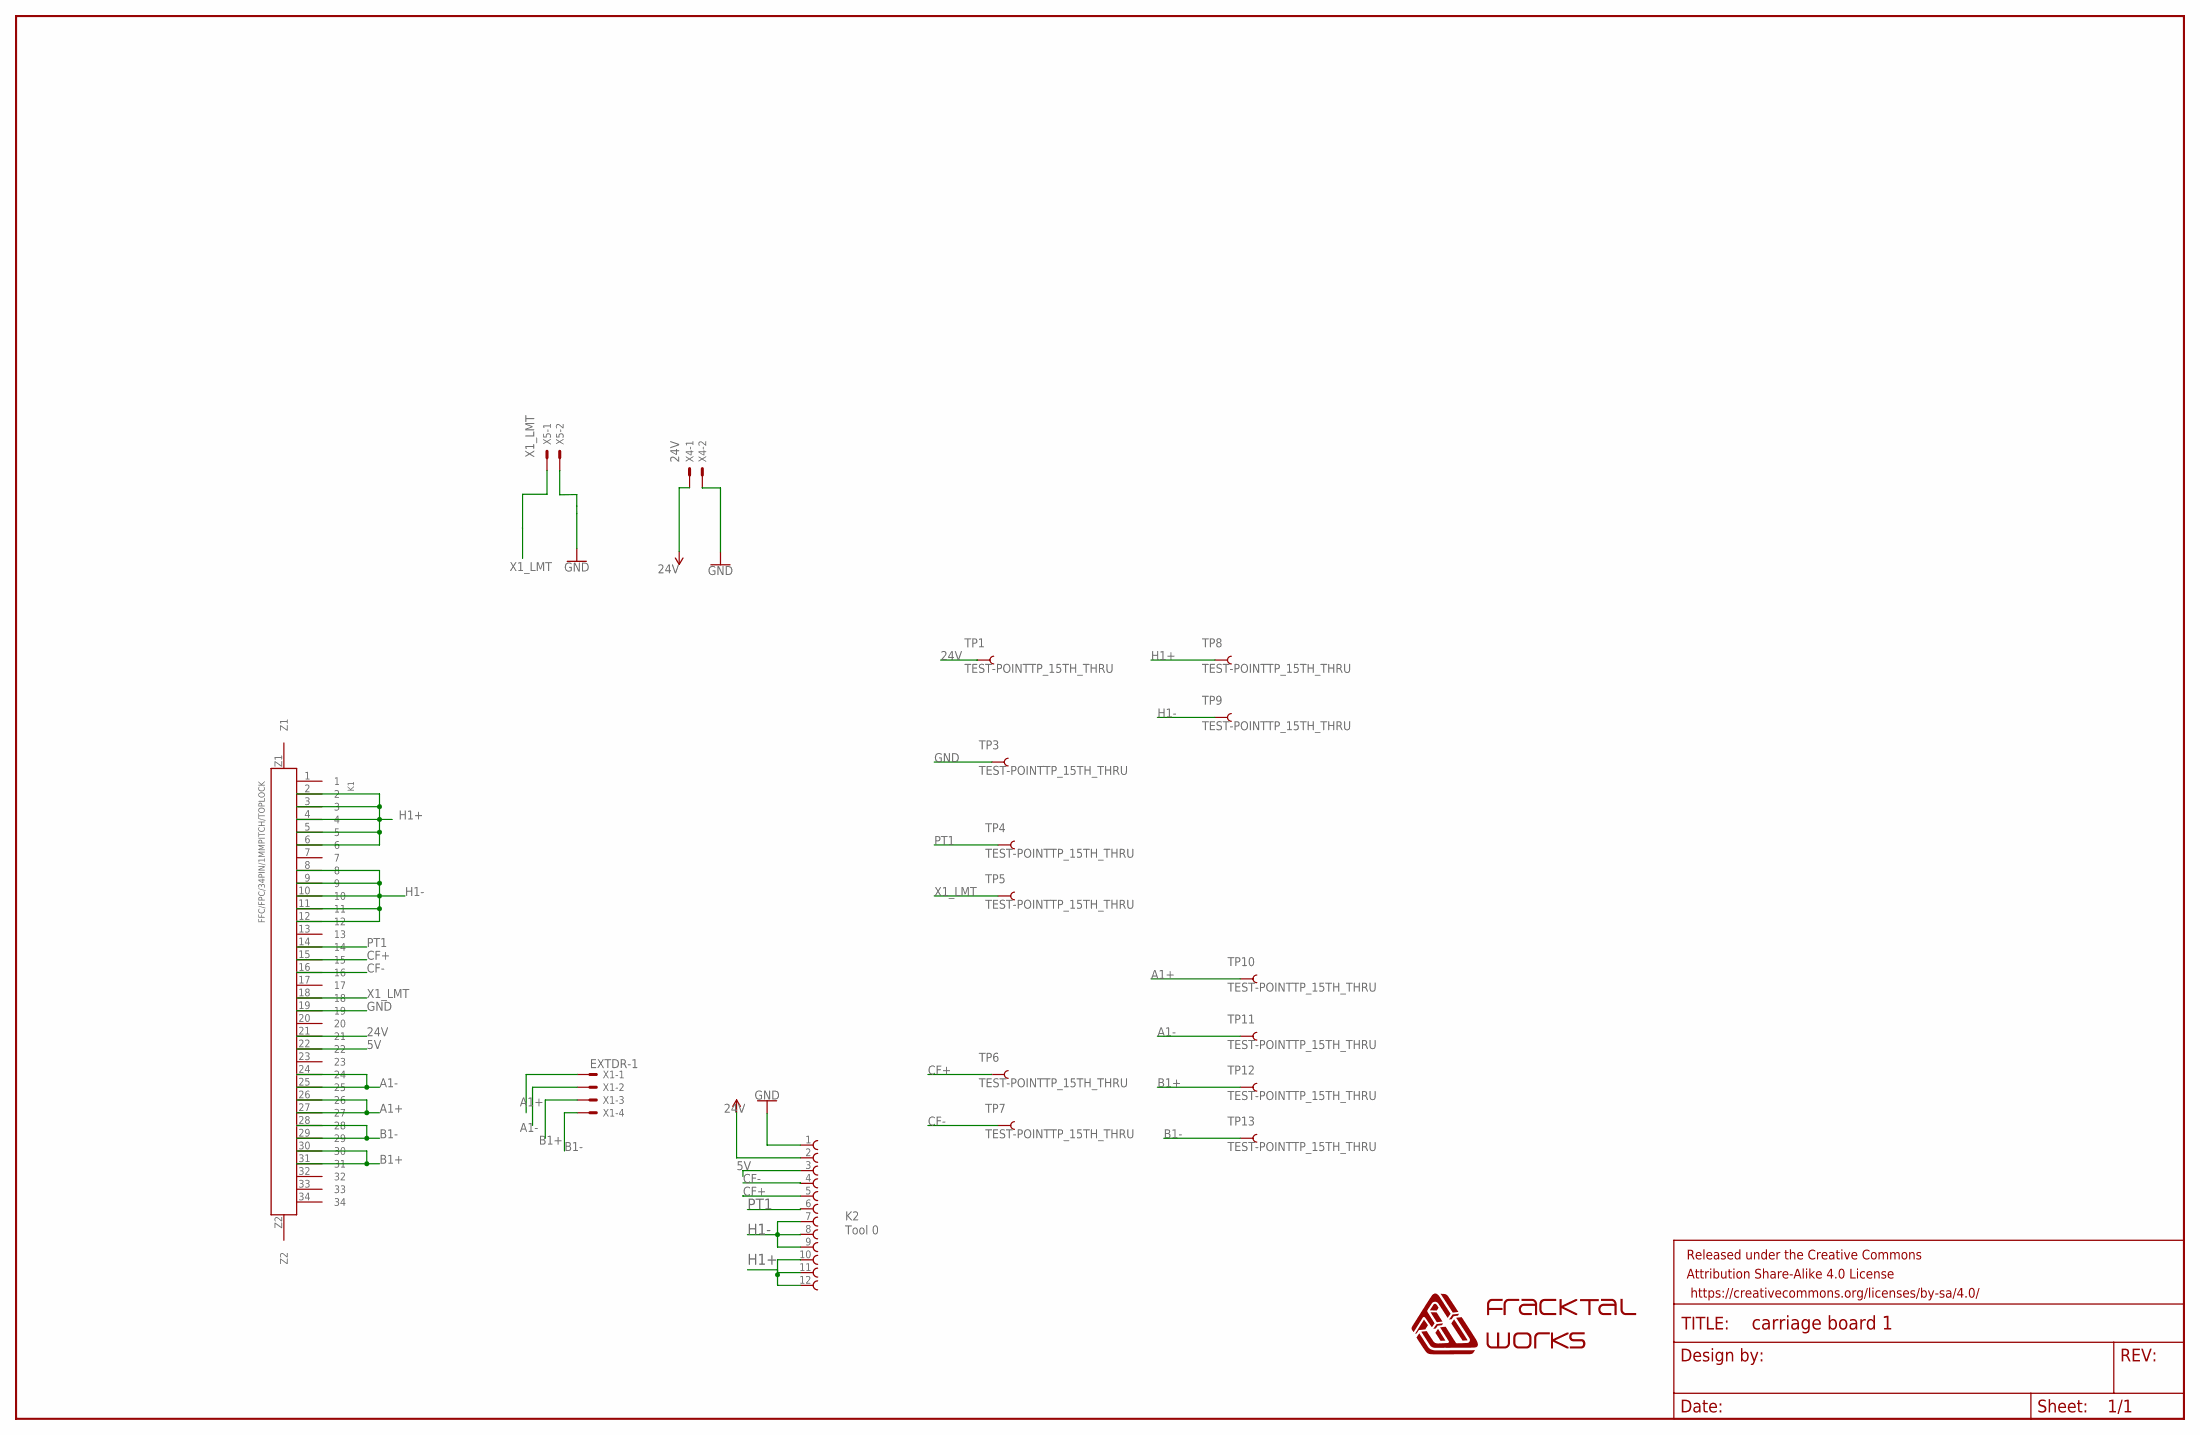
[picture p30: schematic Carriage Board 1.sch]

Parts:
FRAME1: FRAME-LEDGER; CREATIVE_COMMONS
K1: FFC/FPC/34PIN/1MMPITCH/TOPLOCK; 34PIN/1MMPITCH/FFC/FPC
K2: Tool 0; 68611214122
TP1, TP3, TP4, TP5, TP6, TP7, TP8, TP9, TP10, TP11, TP12, TP13: TEST-POINTTP_15TH_THRU; TP_15TH
U$2: FWLOGO
X1: EXTDR-0; JST-XH-04-PACKAGE-LONG-PAD
X4: 24V; JST-XH-02-PACKAGE-LONG-PAD
X5: X_LMT; JST-XH-02-PACKAGE-LONG-PAD

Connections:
5V: K1.22, K2.3
24V: K1.21, K2.2, TP1.P$1, X4.1
A1+: K1.26, K1.27, TP10.P$1, X1.1
A1-: K1.24, K1.25, TP11.P$1, X1.2
B1+: K1.30, K1.31, TP12.P$1, X1.3
B1-: K1.28, K1.29, TP13.P$1, X1.4
CF+: K1.15, K2.5, TP6.P$1
CF-: K1.16, K2.4, TP7.P$1
GND: K1.19, K2.1, TP3.P$1, X4.2, X5.2
H1+: K1.2, K1.3, K1.4, K1.5, K1.6, K2.10, K2.11, K2.12, TP8.P$1
H1-: K1.8, K1.9, K1.10, K1.11, K1.12, K2.7, K2.8, K2.9, TP9.P$1
PT1: K1.14, K2.6, TP4.P$1
X1_LMT: K1.18, TP5.P$1, X5.1

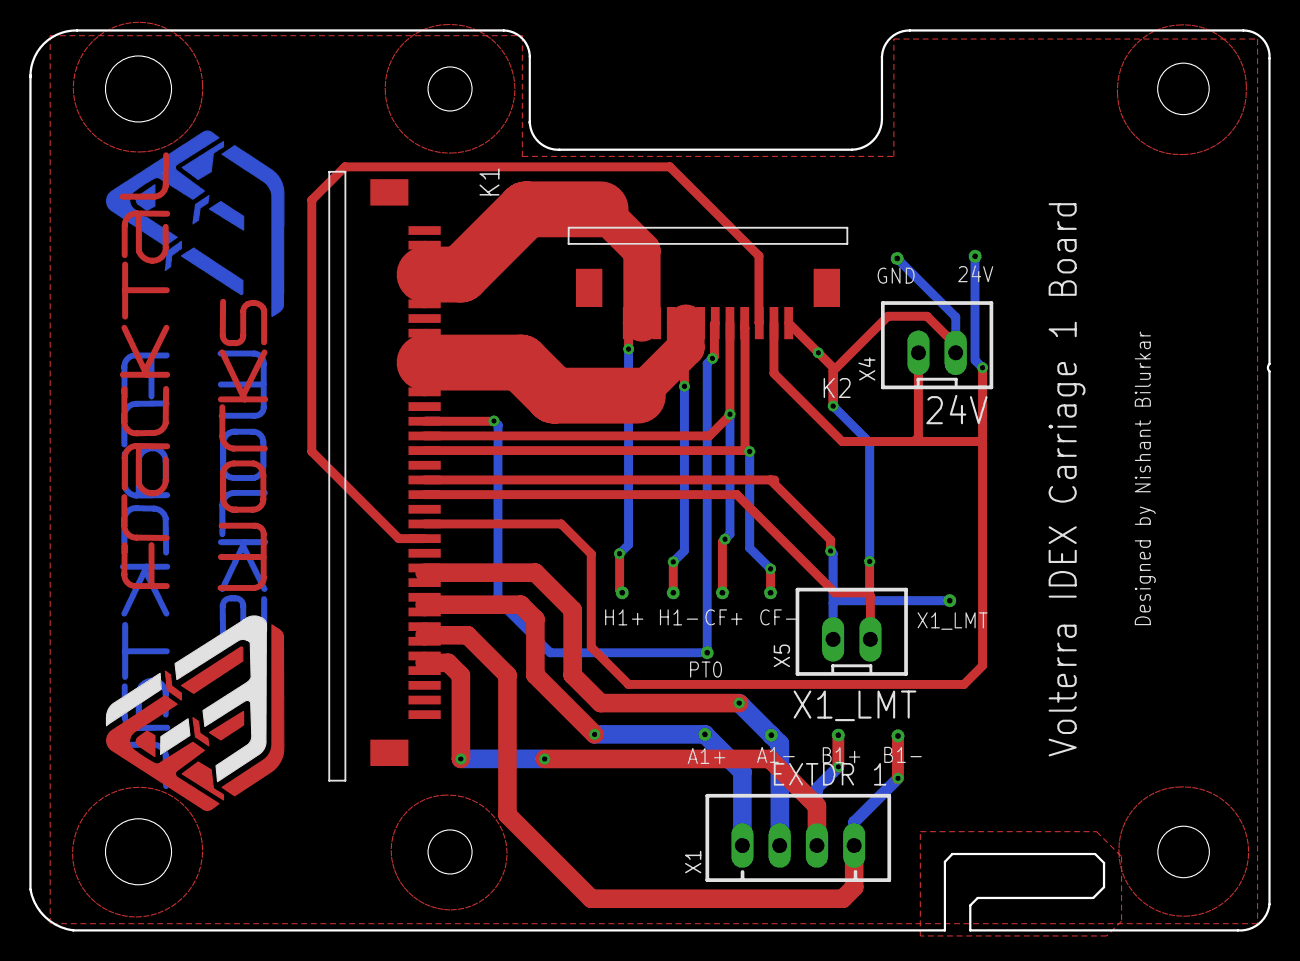
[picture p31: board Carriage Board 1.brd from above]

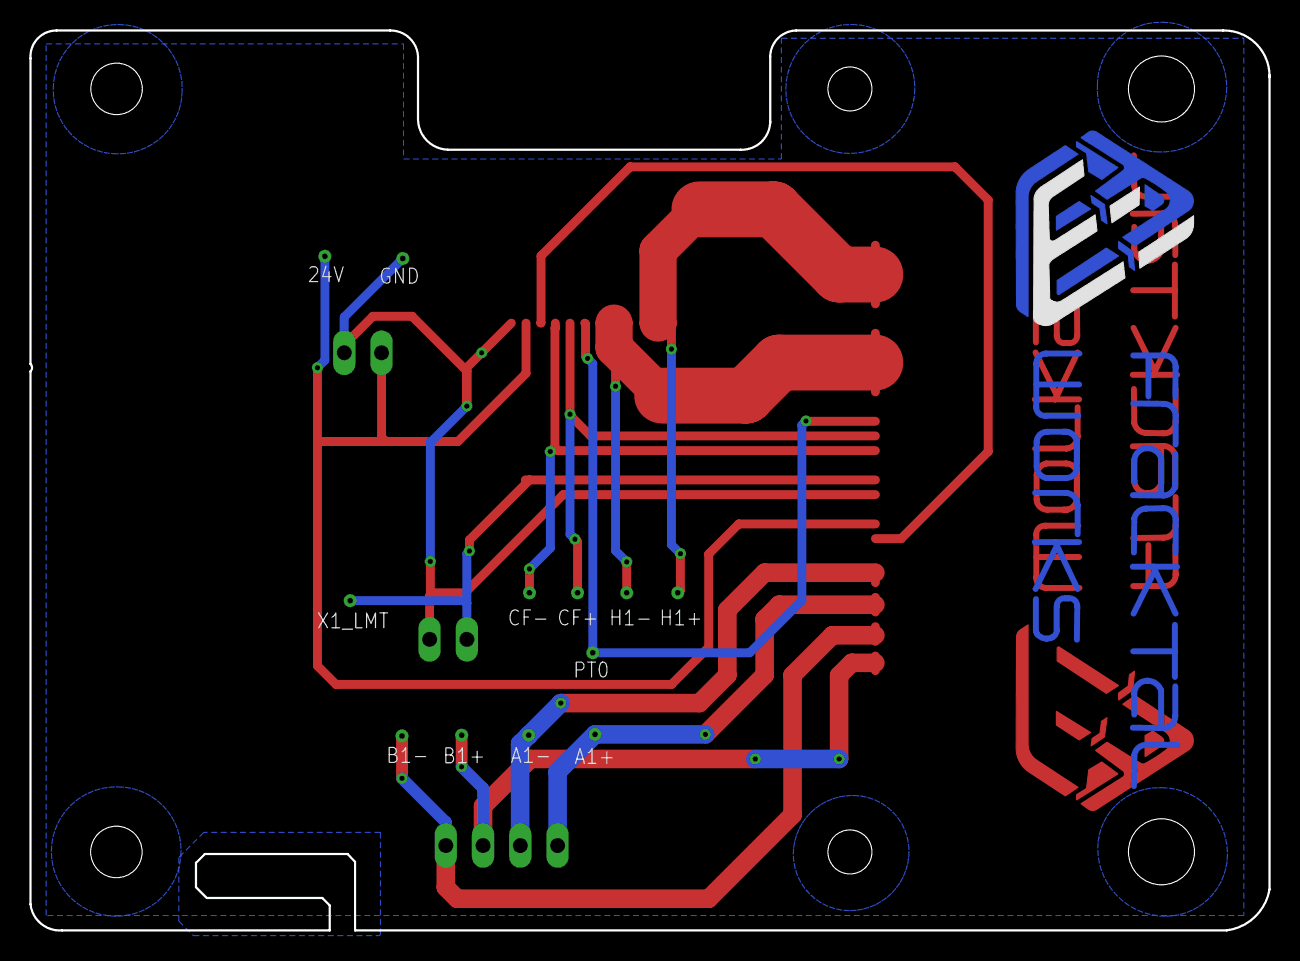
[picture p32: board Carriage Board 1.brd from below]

Board: 2 copper layers, 84.5 x 61.3 mm, 20 parts (12 on the bottom side), 13 nets.

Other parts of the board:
U$1: FWLOGO

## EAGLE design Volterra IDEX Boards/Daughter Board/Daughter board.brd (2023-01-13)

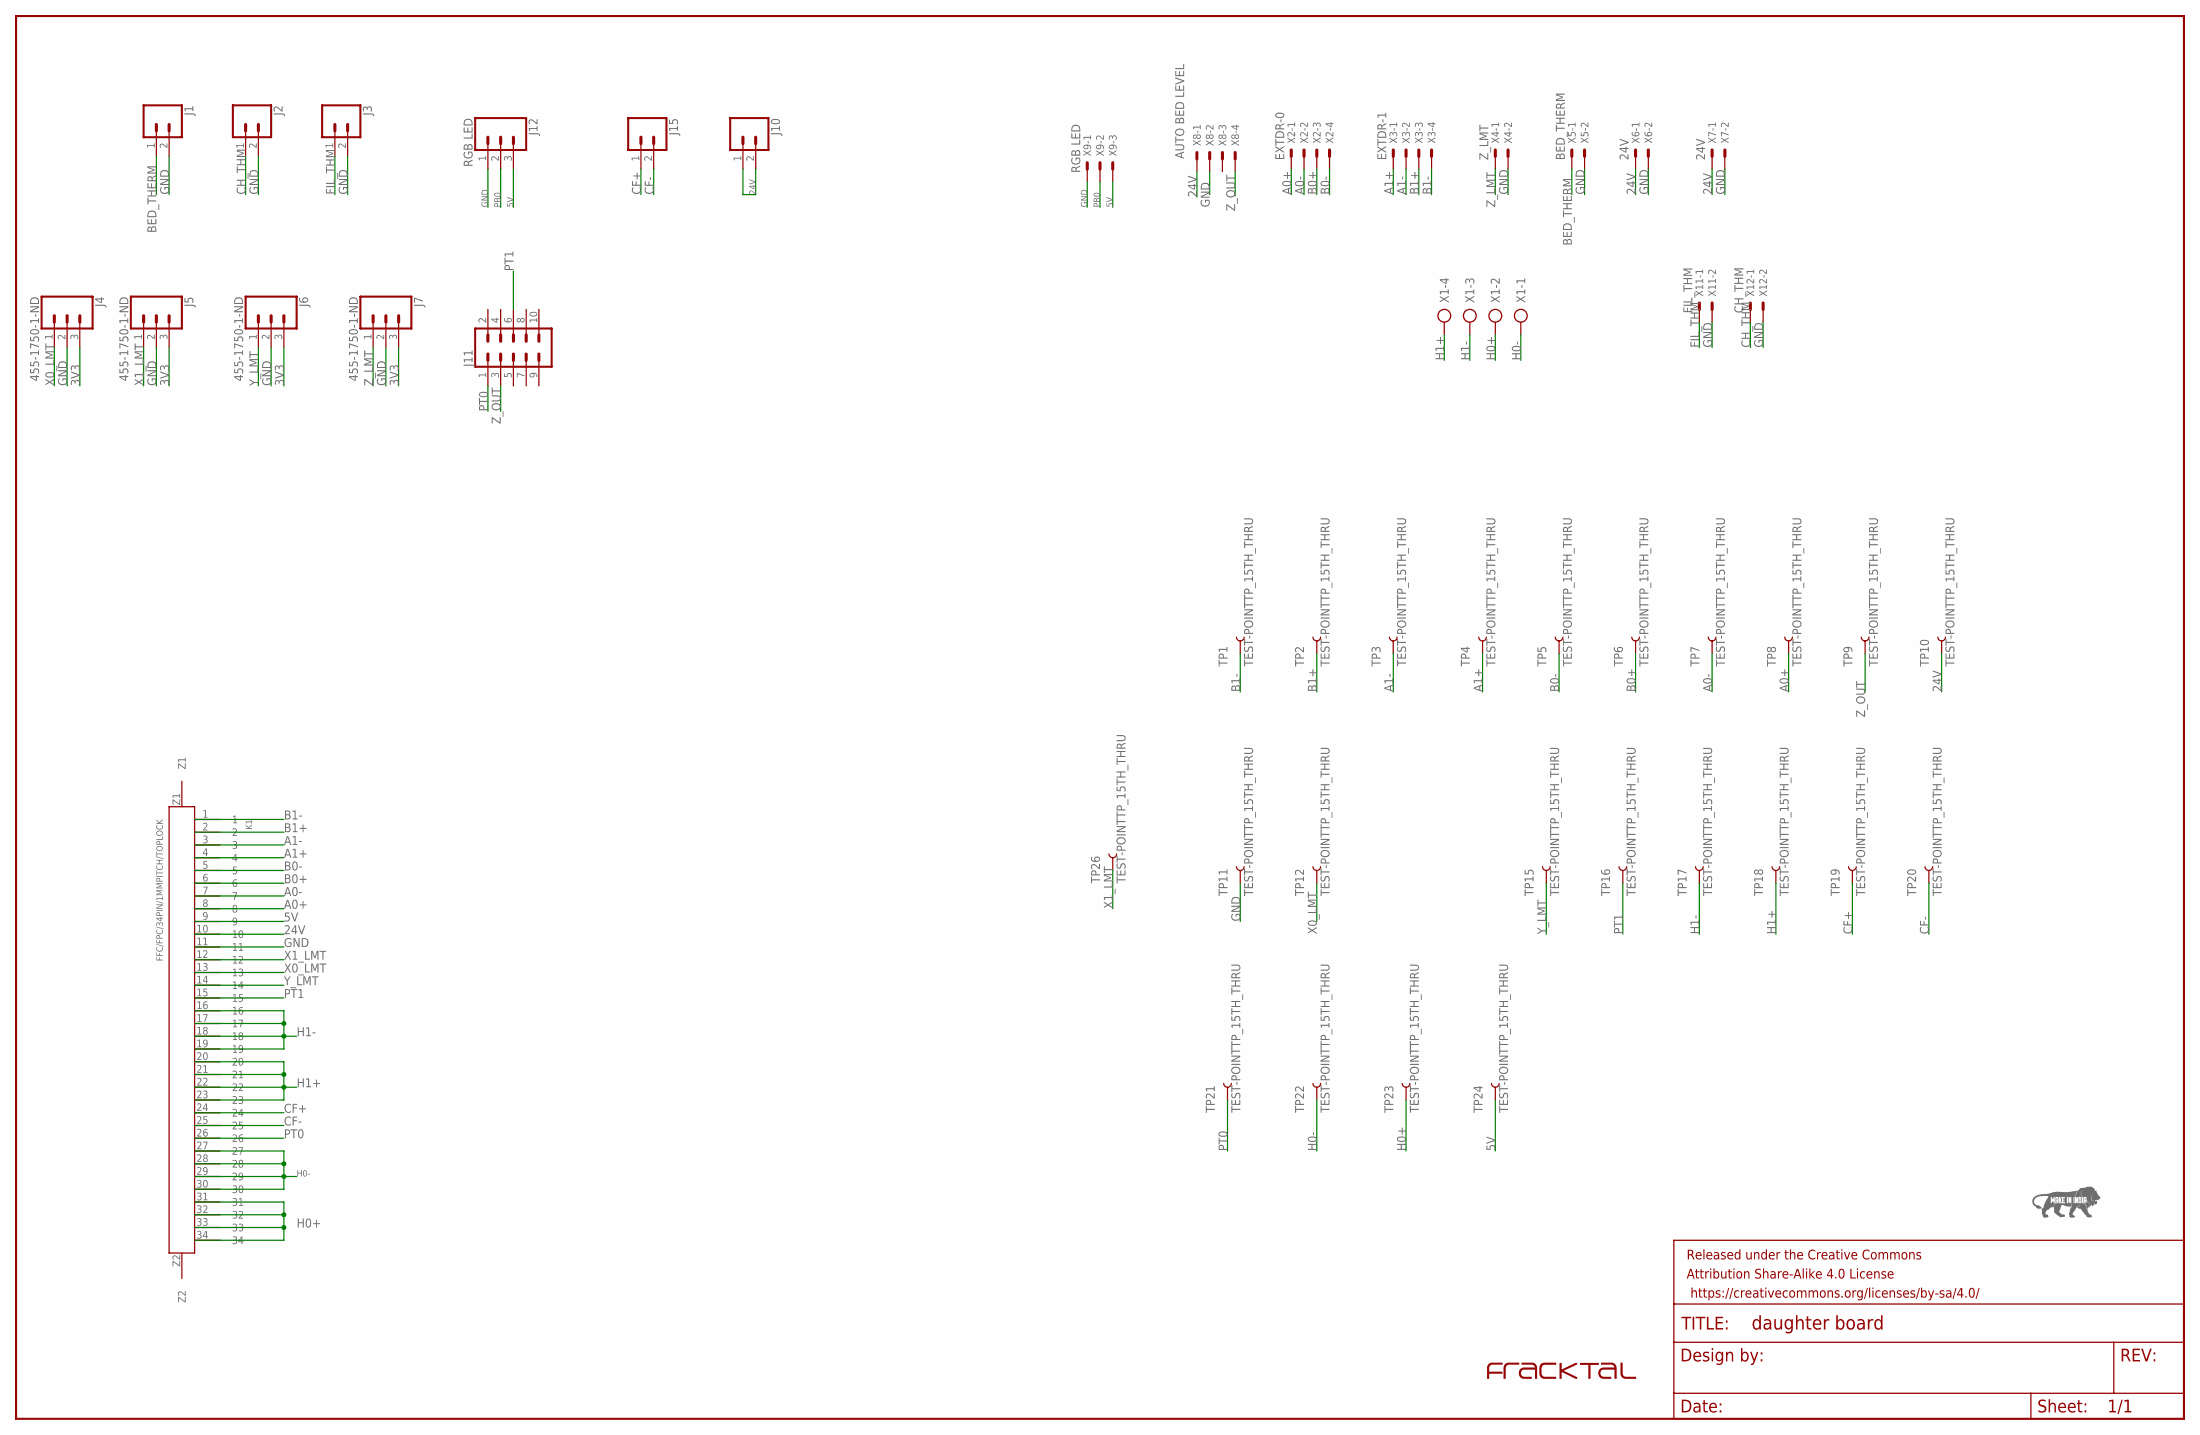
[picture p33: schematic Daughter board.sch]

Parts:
FRAME1: FRAME-LEDGER; CREATIVE_COMMONS
J1, J2, J3, J10, J15: CONN_02; 1X02
J4, J5, J6, J7: 455-1750-1-ND; 1X03
J11: CONN_05X2NO_SILK; 2X5_NOSILK
J12: RGB LED; 1X03
K1: FFC/FPC/34PIN/1MMPITCH/TOPLOCK; 34PIN/1MMPITCH/FFC/FPC
TP1, TP2, TP3, TP4, TP5, TP6, TP7, TP8, TP9, TP10, TP11, TP12, TP15, TP16, TP17, TP18, TP19, TP20, TP21, TP22, TP23, TP24, TP26: TEST-POINTTP_15TH_THRU; TP_15TH
U$1: FRACKTALLOGO
U$2: MAKEININDIA
X1: AK500/4
X2: EXTDR-0; JST-XH-04-PACKAGE-LONG-PAD
X3: EXTDR-1; JST-XH-04-PACKAGE-LONG-PAD
X4: Z_LMT; JST-XH-02-PACKAGE-LONG-PAD
X5: BED_THERM; JST-XH-02-PACKAGE-LONG-PAD
X6, X7: 24V; JST-XH-02-PACKAGE-LONG-PAD
X8: AUTO BED LEVELING; JST-XH-04-PACKAGE-LONG-PAD
X9: RGB LED; JST-XH-03-PACKAGE-LONG-PAD
X11: FIL_THM; JST-XH-02-PACKAGE-LONG-PAD
X12: CH_THM; JST-XH-02-PACKAGE-LONG-PAD

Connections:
3V3: J4.3, J5.3, J6.3, J7.3
5V: J12.3, K1.9, TP24.P$1, X9.3
24V: J10.1, J10.2, K1.10, TP10.P$1, X6.1, X7.1, X8.1
A0+: K1.8, TP8.P$1, X2.1
A0-: K1.7, TP7.P$1, X2.2
A1+: K1.4, TP4.P$1, X3.1
A1-: K1.3, TP3.P$1, X3.2
B0+: K1.6, TP6.P$1, X2.3
B0-: K1.5, TP5.P$1, X2.4
B1+: K1.2, TP2.P$1, X3.3
B1-: K1.1, TP1.P$1, X3.4
BED_THERM: J1.1, X5.1
CF+: J15.1, K1.24, TP19.P$1
CF-: J15.2, K1.25, TP20.P$1
CH_THM: J2.1, X12.1
FIL_THM: J3.1, X11.1
GND: J1.2, J2.2, J3.2, J4.2, J5.2, J6.2, J7.2, J12.1, K1.11, TP11.P$1, X4.2, X5.2, X6.2, X7.2, X8.2, X9.1, X11.2, X12.2
H0+: K1.31, K1.32, K1.33, K1.34, TP23.P$1, X1.2
H0-: K1.27, K1.28, K1.29, K1.30, TP22.P$1, X1.1
H1+: K1.20, K1.21, K1.22, K1.23, TP18.P$1, X1.4
H1-: K1.16, K1.17, K1.18, K1.19, TP17.P$1, X1.3
PB0: J12.2, X9.2
PT0: J11.1, K1.26, TP21.P$1
PT1: J11.6, K1.15, TP16.P$1
X0_LMT: J4.1, K1.13, TP12.P$1
X1_LMT: J5.1, K1.12, TP26.P$1
Y_LMT: J6.1, K1.14, TP15.P$1
Z_LMT: J7.1, X4.1
Z_OUT: J11.3, TP9.P$1, X8.4

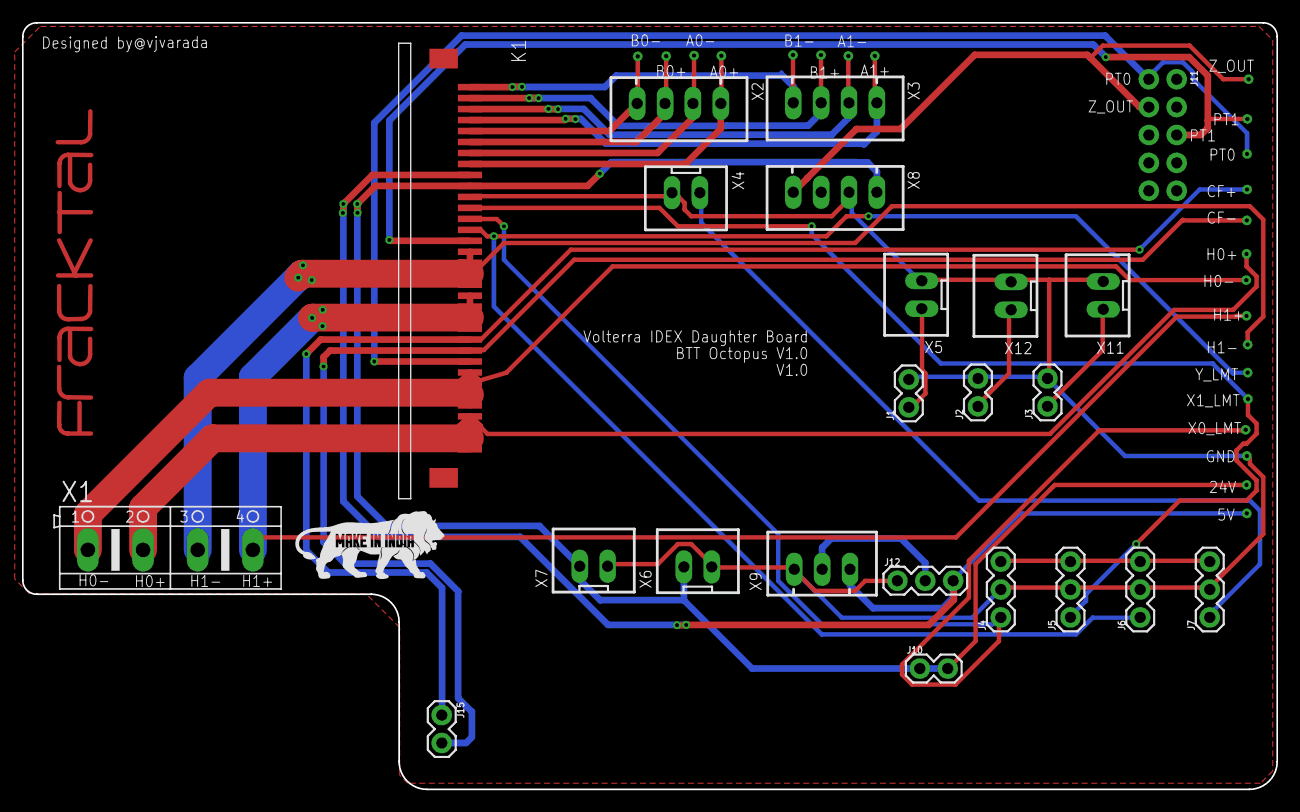
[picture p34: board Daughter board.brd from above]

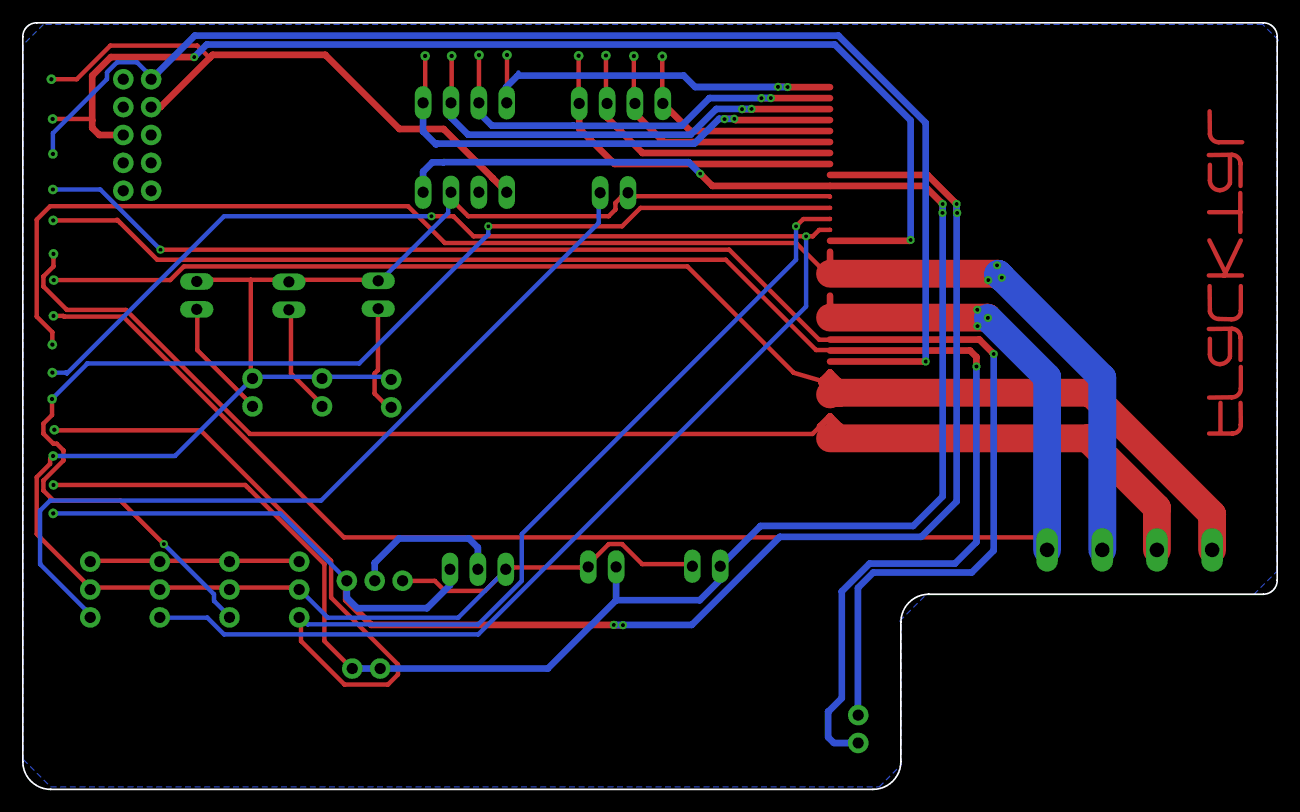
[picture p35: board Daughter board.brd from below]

Board: 2 copper layers, 114.3 x 69.8 mm, 49 parts (23 on the bottom side), 29 nets.

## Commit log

2023-01-11 Volterra IDEX PCB files
    Uploaded Chassis, Carriage 0 and Carriage 1 boards
    [Carriage 1.brd, Carriage 1.sch, Carriage Board 0.brd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]
2023-01-12 Daughter board added
    [0411-2.iam, 1.iam, 1.ipt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]
2023-01-12 Switching of carriage board numbering, changing extruder FFC pins and fixing routings
    [Carriage 0.brd, Carriage 0.sch, Carriage Board 1.brd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]
2023-01-12 Updated Daughter board schematic and other boards
    [Carriage 0.brd, Carriage 0.sch, Carriage Board 1.brd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]
2023-01-12 DRC checked of Chassis, Carriage 1 & 2, and created CAM files
    [Carriage 0.brd, Carriage Board 1.brd, Chassis board.brd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]
2023-01-13 Added Daughter Board
    [Daughter board.brd, Daughter board.sch]
2023-01-13 Board files added
    [Carriage 0.brd, Carriage 0.sch, Carriage Board 1.brd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]
2023-01-13 Updated Chassis, Carriage 0 and 1 CAM and gerber files
    [copper_bottom.gbr, copper_top.gbr, drill_1_16.xln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]
2023-02-06 Updated Chassis Board mount holes and re-routing
    [Chassis board.brd, Chassis board.sch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]
2023-03-18 Volterra IDEX Electronics Documentation
2023-04-04 Attached manual

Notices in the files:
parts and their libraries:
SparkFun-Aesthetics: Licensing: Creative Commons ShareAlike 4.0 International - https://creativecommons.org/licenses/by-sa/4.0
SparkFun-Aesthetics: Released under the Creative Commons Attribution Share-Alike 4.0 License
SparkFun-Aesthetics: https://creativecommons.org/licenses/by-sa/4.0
